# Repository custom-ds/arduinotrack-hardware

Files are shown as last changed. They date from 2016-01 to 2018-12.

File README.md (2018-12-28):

# ArduinoTrack APRS Tracker
The Project: Traveler ArduinoTrack flight controller is an Arduino-compatible board that includes a GPS, temp/pressure sensor, and options for a VHF transmitter module or a off-board transmitter.

For more information about the ArduinoTrack, visit the [Project: Traveler](https://www.projecttraveler.org/arduinotrack/arduinotrack-controller) website.

Firmware for the ArduinoTrack must be programmed via a hardware programmer.

[ArduinoTrack Firmware](https://github.com/custom-ds/arduinotrack-firmware)

## Buy an ArduinoTrack
Assembled ArduinoTracks can be purchased online from [Custom Digital Services](https://www.customdigitalservices.net/high-altitude-ballooning/buy-an-arduinotrack).

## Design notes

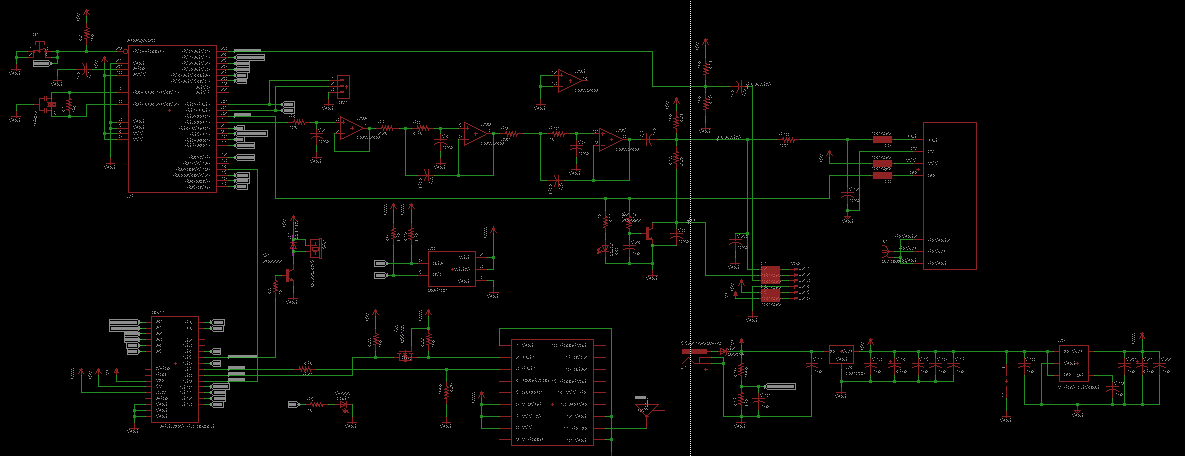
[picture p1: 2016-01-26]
ArduinoTrack Shield/arduinotrack_shield_v111-schematic.png

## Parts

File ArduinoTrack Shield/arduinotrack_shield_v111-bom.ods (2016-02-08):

Qty | Value | Device | Package | Parts | Description | DIGIKEY | SPARKFUN
1 |  | MA03-1 | MA03-1 | SV1 | PIN HEADER | 952-2264-ND
1 |  | TAC_SWITCHSMD | TACTILE_SWITCH_SMD | S1 | Momentary Switch | CKN9104CT-ND
14 | .1uF | C-USC0805 | C0805 | C1, C7, C9, C10, C11, C13, C15, C16, C17, C18, C19, C20, C22, C24 | CAPACITOR, American symbol | 311-1361-1-ND
1 | 100 | R-US_R0805 | R0805 | R18 | RESISTOR, American symbol | 311-100ARCT-ND
2 | 100k | R-US_R0805 | R0805 | R16, R20 | RESISTOR, American symbol | 311-100KCRCT-ND
7 | 10k | R-US_R0805 | R0805 | R2, R4, R14, R15, R22, R23, R24 | RESISTOR, American symbol | 311-10.0KCRCT-ND
6 | 10nF | C-USC0805 | C0805 | C2, C4, C6, C8, C12, C23 | CAPACITOR, American symbol | 399-1158-1-ND
8 | 160 ohm | SM-1206 | SM-1206 | L1, L2, L3, L4, L5, L6, L7, L8 | INDUCTOR | 240-2411-1-ND
1 | 16MHz | RESONATOR16MHZ | RESONATOR-SMD | Y1 | Resonator | 478-5420-1-ND
1 | 1M | R-US_R0805 | R0805 | R1 | RESISTOR, American symbol | 311-1.0MARCT-ND
5 | 1k | R-US_R0805 | R0805 | R3, R5, R10, R11, R12 | RESISTOR, American symbol | 311-1.0KARCT-ND
2 | 2.2k | R-US_R0805 | R0805 | R7, R13 | RESISTOR, American symbol | 311-2.2KARCT-ND
2 | 2N2222 | BC817-16LT1SMD | SOT23-BEC | Q1, Q2 | NPN Transistor | MMBT2222AFSCT-ND
1 | 390 | R-US_R0805 | R0805 | R9 | RESISTOR, American symbol | 311-390ARCT-ND
3 | 4.7k | R-US_R0805 | R0805 | R6, R8, R19 | RESISTOR, American symbol | 311-4.7KARCT-ND
2 | 47k | R-US_R0805 | R0805 | R17, R21 | RESISTOR, American symbol | 311-47.0KCRCT-ND
2 | 47nF | C-USC0805 | C0805 | C3, C5 | CAPACITOR, American symbol | 399-1166-1-ND
2 | 47uF | CPOL-US153CLV-0605 | 153CLV-0605 | C14, C21 | POLARIZED CAPACITOR, American symbol | PCE3842CT-ND
1 | 5.5x2.1mm Barrel | POWER_JACKSMD | POWER_JACK_SMD | J1 | Power Jack | CP-002AHPJCT-ND
1 | ARDUINO_R3_SHIELD | ARDUINO_R3_SHIELD | UNO_R3_SHIELD | SH11 | Shield form compatible with the Arduino Uno R3. |  | PRT-10007
1 | ATMega328 | MEGA8-AI | TQFP32-08 | U7 | MICROCONTROLLER | ATMEGA328P-15AZCT-ND
1 | B220/A | B340A | SMA-DIODE | D2 | Schottky Diode | 641-1258-1-ND
1 | BMP180 | BMP180 | BMP180 | U8 | BOSCH BMP180 DIGITAL BAROMETRIC PRESSURE SENSOR |  | COM-11823
1 | BSS138 | BSS138 | BSS138 | Q3 | BSS138 | BSS138CT-ND
1 | BU-SMA-H | BU-SMA-H | BU-SMA-H | X1 | FEMALE SMA CONNECTOR | CONSMA001-ND
1 | BUZZERNS | BUZZERNS | BUZZER-12MM-NS | SG1 | Buzzer 12mm | 102-1155-ND
1 | GPS_ANT_SMDBAR | GPS_ANT_SMDBAR | 1575AT43A40 | ANT1 | 1.575 GHz GPS Antenna Johanson Technology | 712-1003-1-ND
1 | Green | LEDCHIPLED_1206 | CHIPLED_1206 | LED1 | LED | 160-1169-1-ND
1 | LL4148 | DIODE-MINIMELF | MINIMELF | D1 | DIODE | 568-1749-1-ND
1 | LM1086 | LM1086TO263 | TO263 | U4 |  | LM1086ISX-5.0/NOPBCT-ND
1 | MCP6L04T-E/SL | MCP6L04T-E/SL | SO14 | U9 | Rail-to-Rail Output Operational Amplifiers | MCP6L04T-E/SLCT-ND
1 | HX1-144.390-3 | RADIOMETRIX-HX1 | RADIOMETRIX-HX1 | U5
1 | Red | LEDCHIPLED_1206 | CHIPLED_1206 | LED2 | LED | 160-1405-1-ND
1 | UBLOX MAX-M8Q | UBLOX_MAX | UBLOX_MAX | U3 | UBLOX MAX
1 | VHF | 22-05-7068-06 | 7395-06 | J2 | CONNECTOR | WM4304-ND
1 | V_REG_LDOSMD | V_REG_LDOSMD | SOT23-5 | U6 | Voltage Regulator LDO | LP3985IM5-3.3/NOPBCT-ND

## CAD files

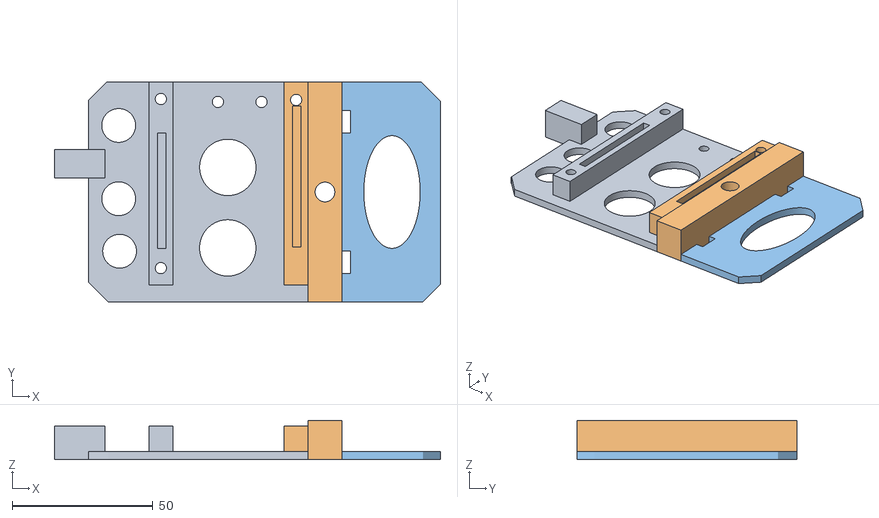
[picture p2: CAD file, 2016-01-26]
Cases/combined/combined.stl
137.0 x 78.0 x 14.0

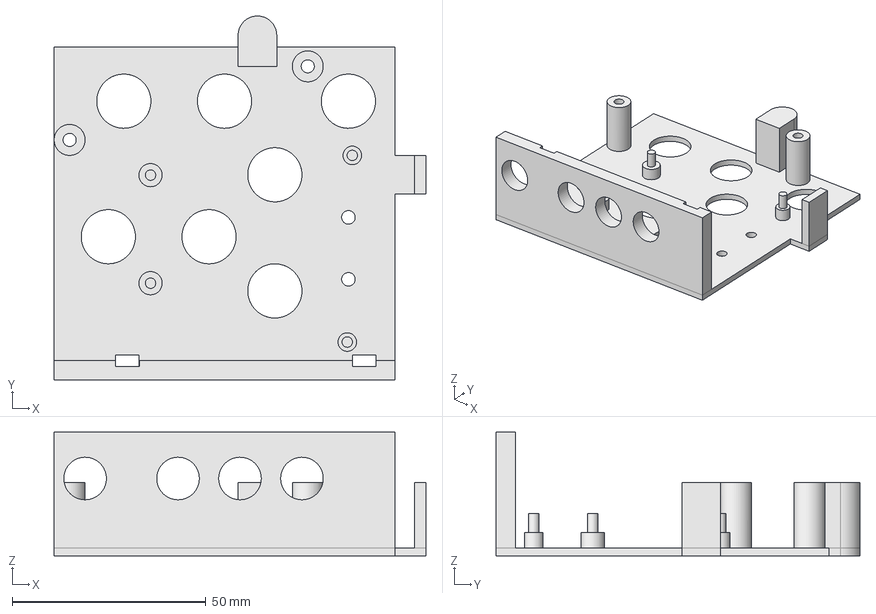
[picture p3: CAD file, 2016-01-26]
Cases/Open Frame for Shield.FCStd
96.0 x 94.0 x 32.0 mm

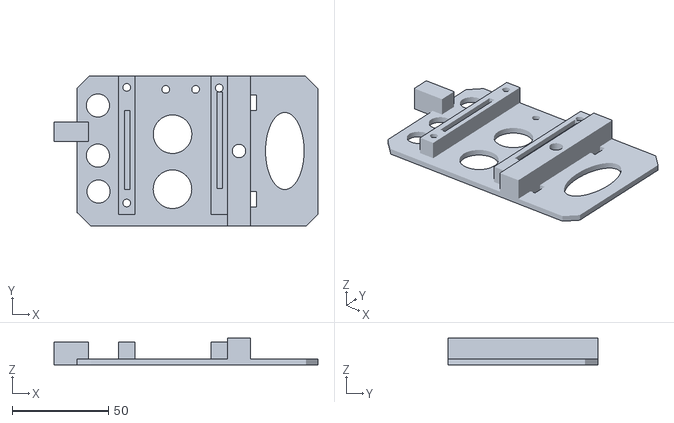
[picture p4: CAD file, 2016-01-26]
Cases/combined/combined2.stl
137.0 x 78.0 x 14.0

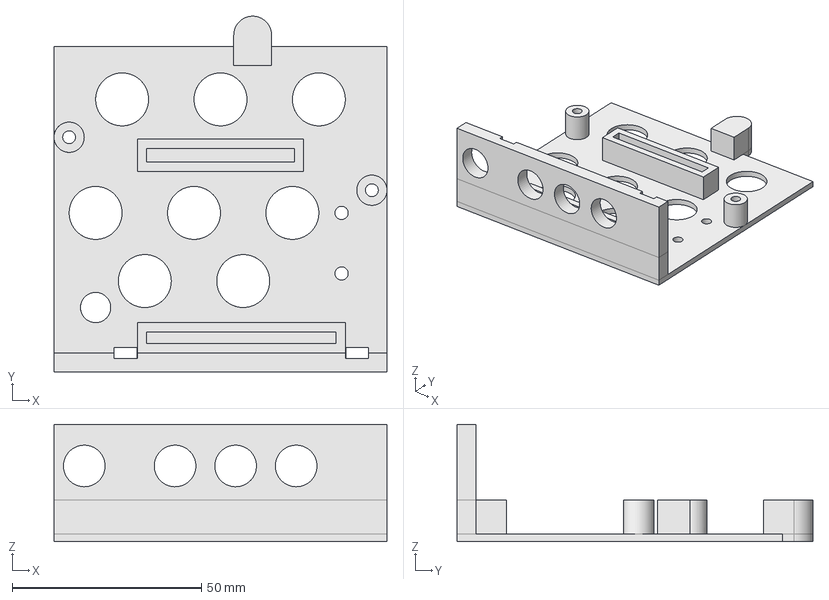
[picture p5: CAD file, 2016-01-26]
Cases/Open Frame for Combined.FCStd
88.0 x 94.0 x 31.0 mm

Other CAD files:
Cases/Open Frame for Combined.stl
Cases/Open Frame for Shield.stl

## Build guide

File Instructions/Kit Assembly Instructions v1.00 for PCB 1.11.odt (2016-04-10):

ArduinoTrack Assembly

Version 1.0 for PCB Version 1.11

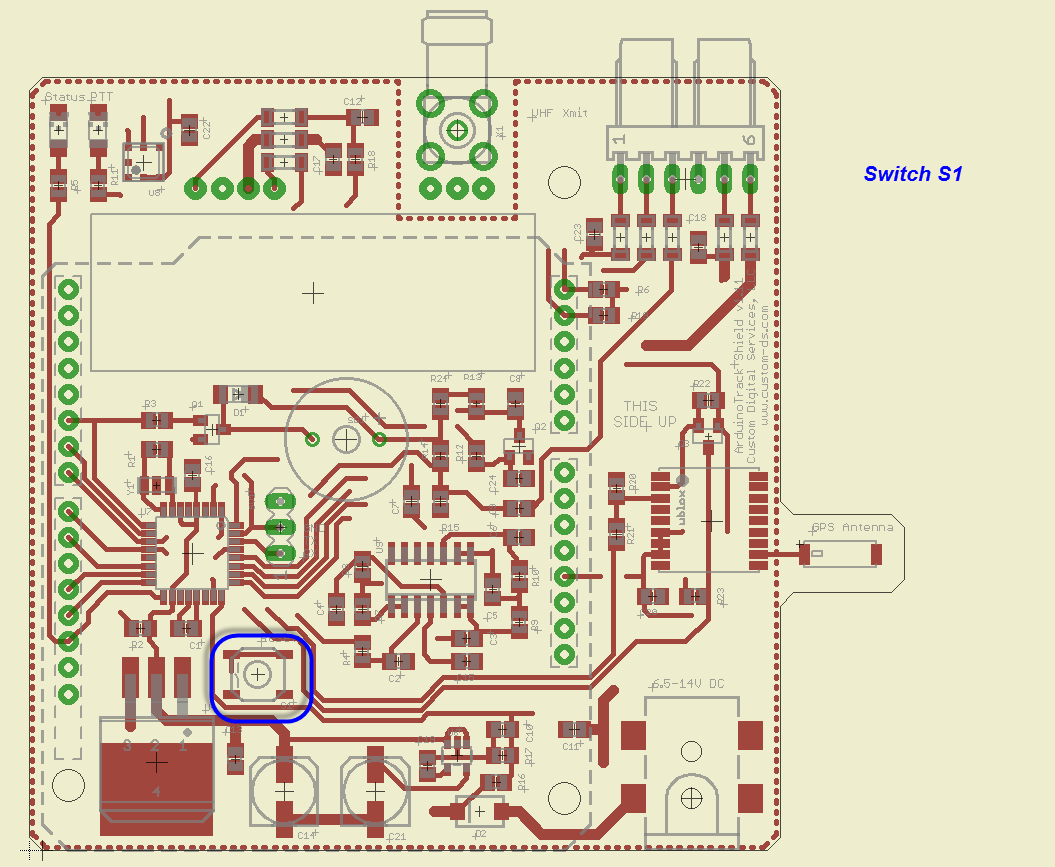
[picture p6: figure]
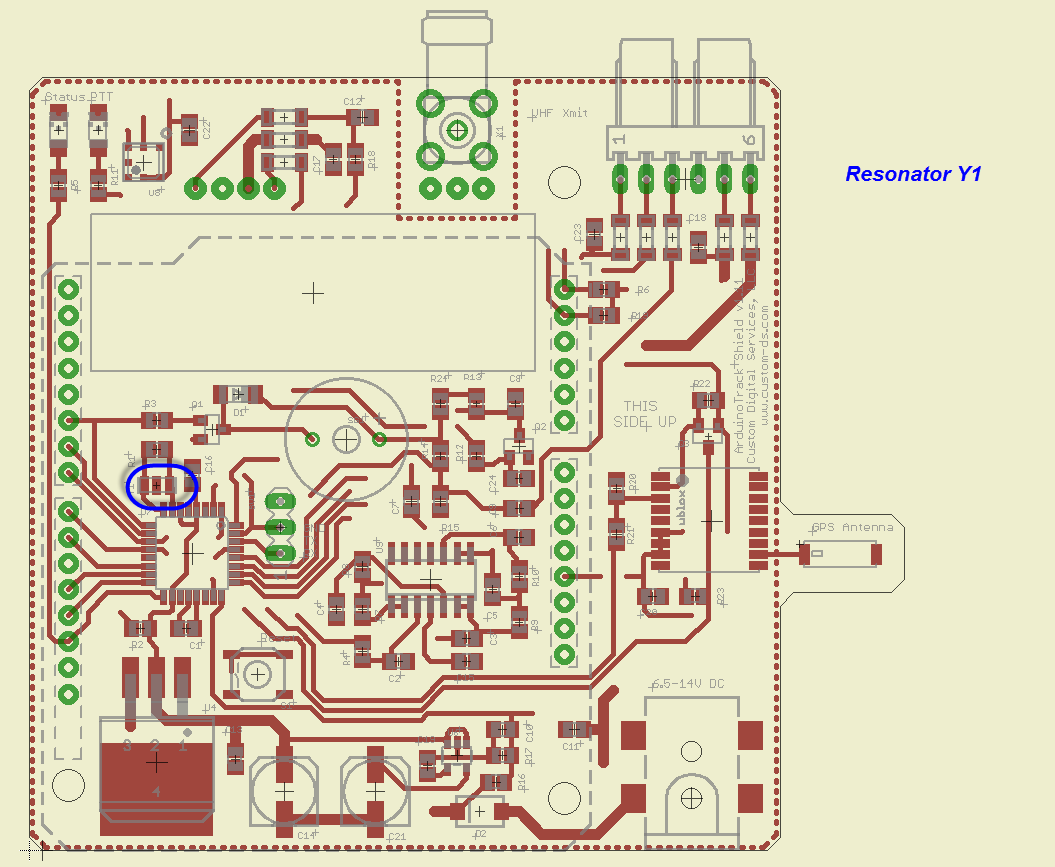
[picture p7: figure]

Switch S1 | Resonator Y1

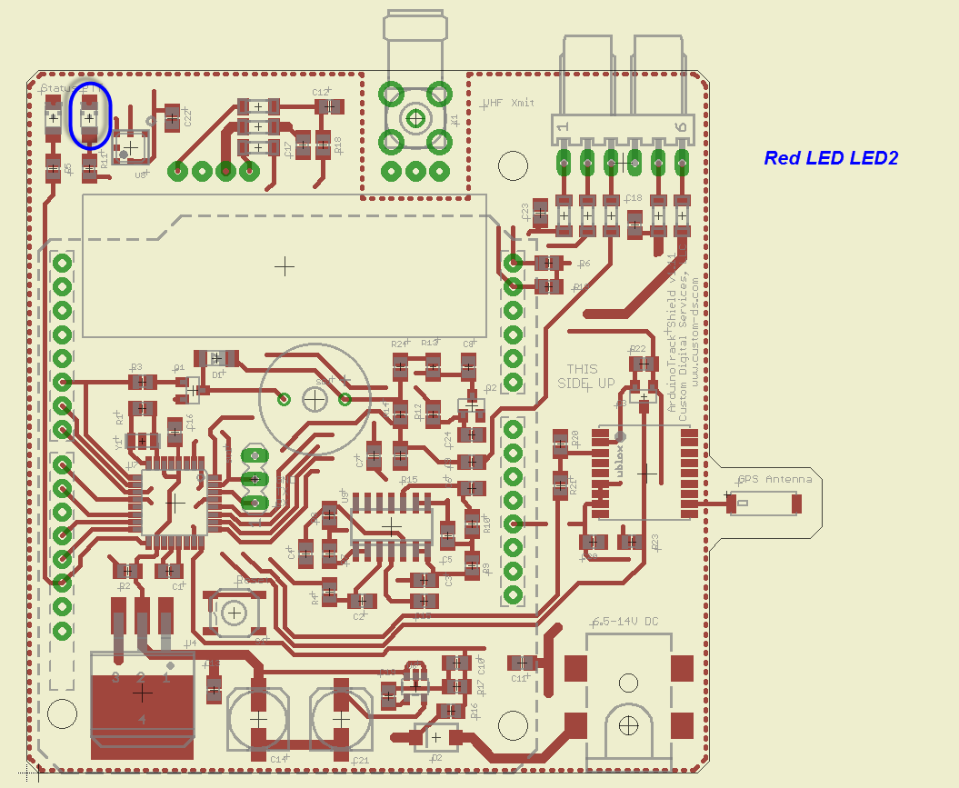
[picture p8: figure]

Green LED LED1 | Red LED LED2

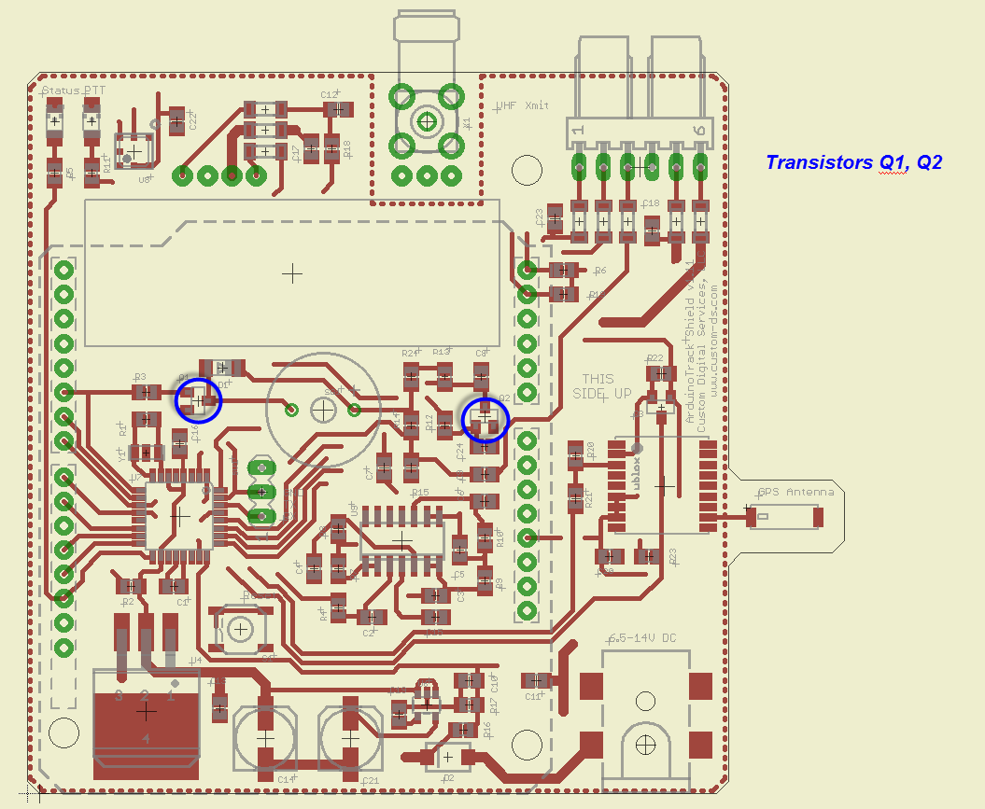
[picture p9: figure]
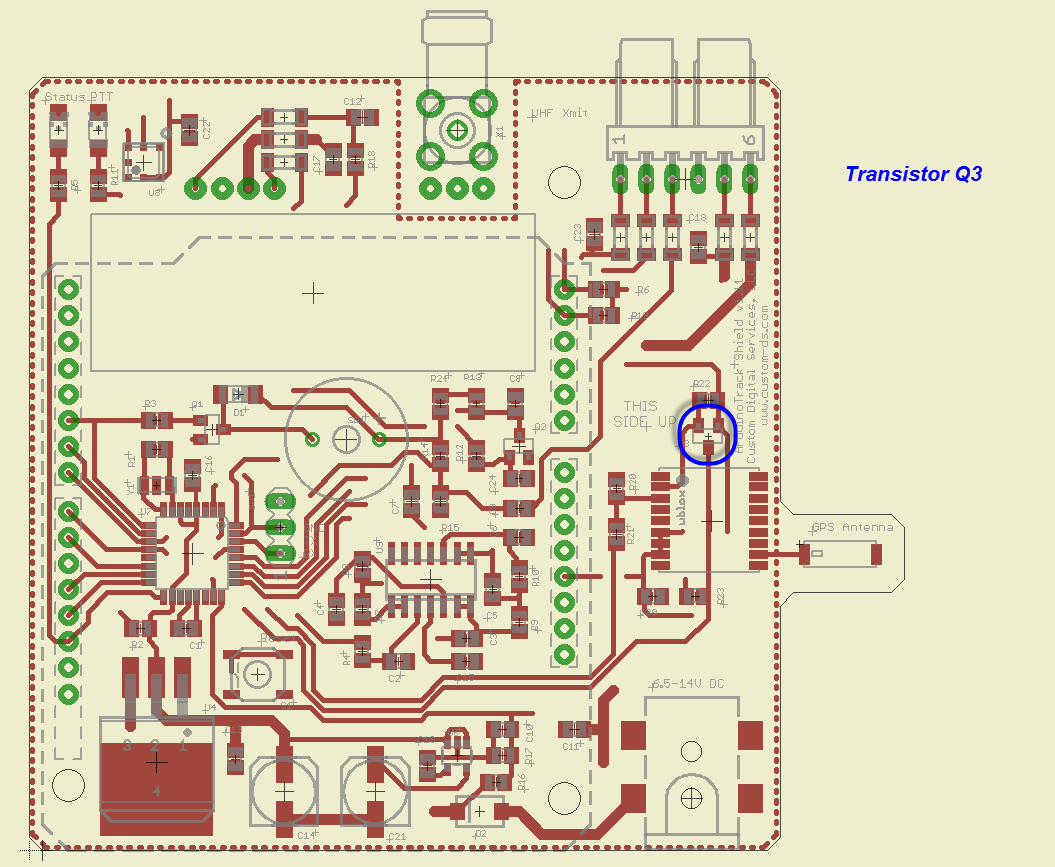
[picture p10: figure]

Transistors Q1, Q2 | FET Transistor Q3

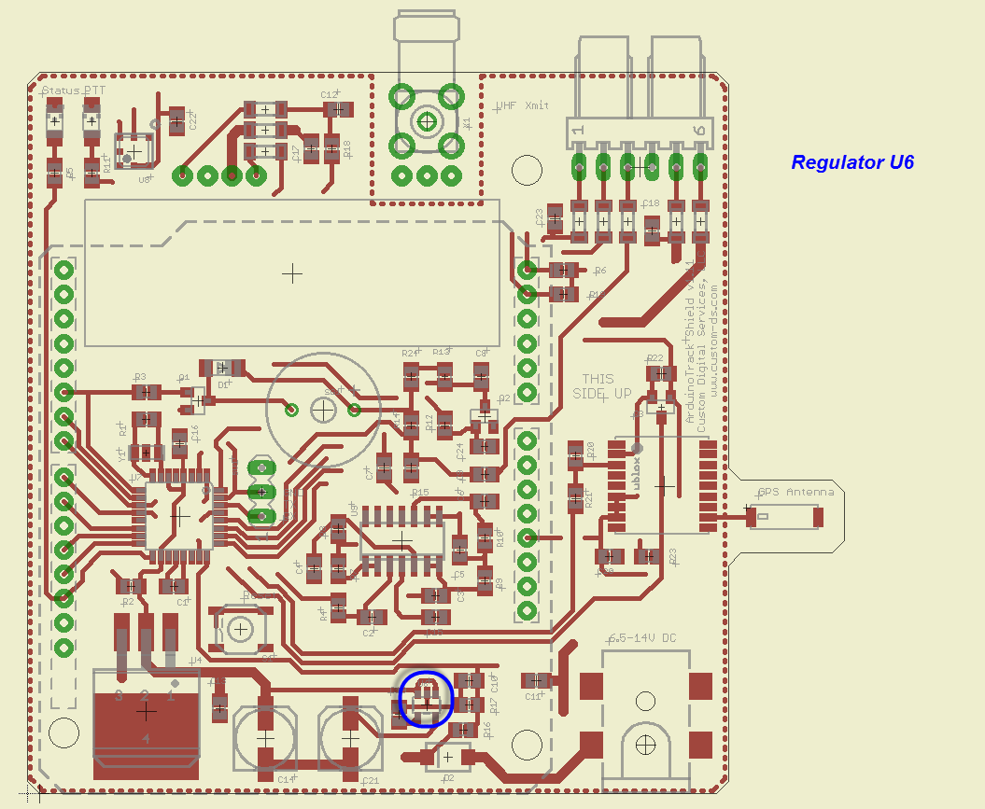
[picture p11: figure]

3.3V Regulator U6 | GPS Antenna ANT1

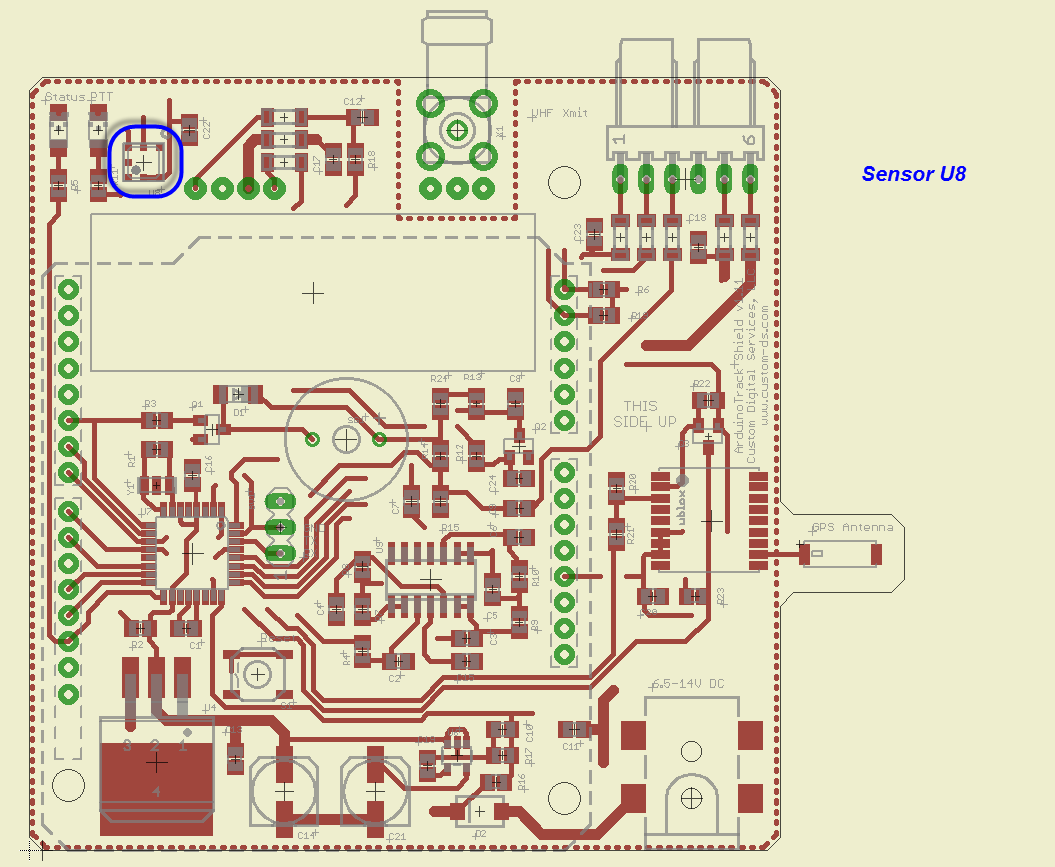
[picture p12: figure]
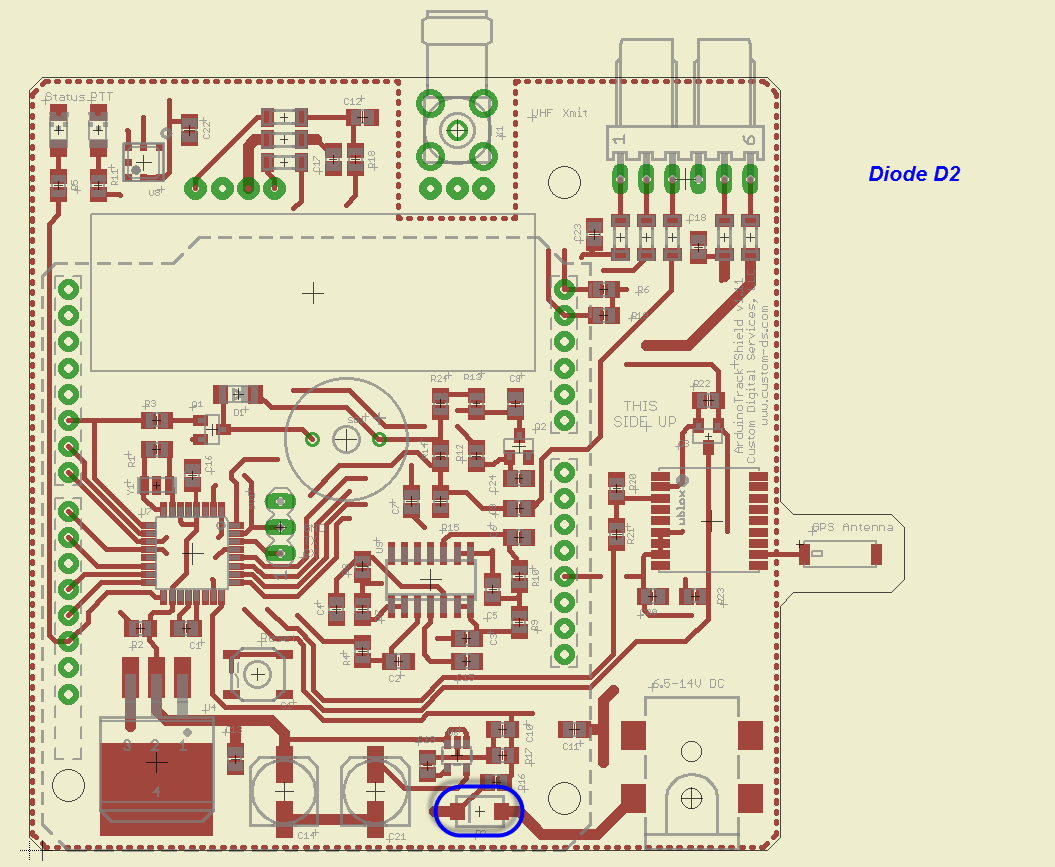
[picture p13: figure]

BMP180 Temp/Baro Sensor U8 | Schottky Protection Diode D2

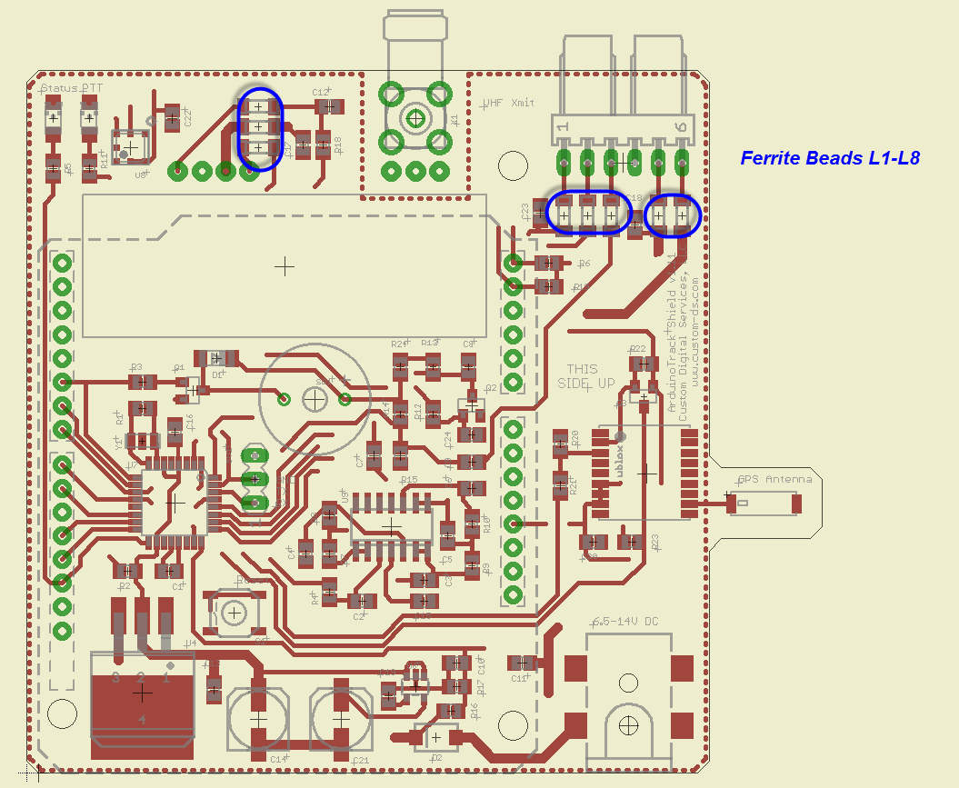
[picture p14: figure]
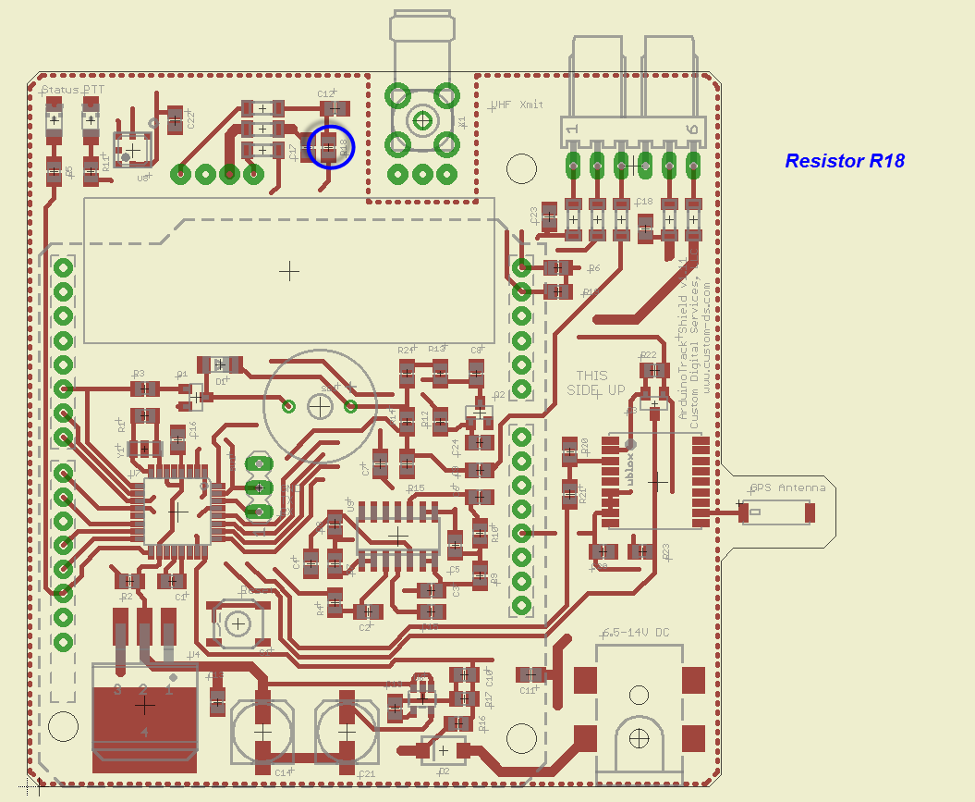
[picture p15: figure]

Ferrite Beads L1-L8 | 100Ω Resistor R18

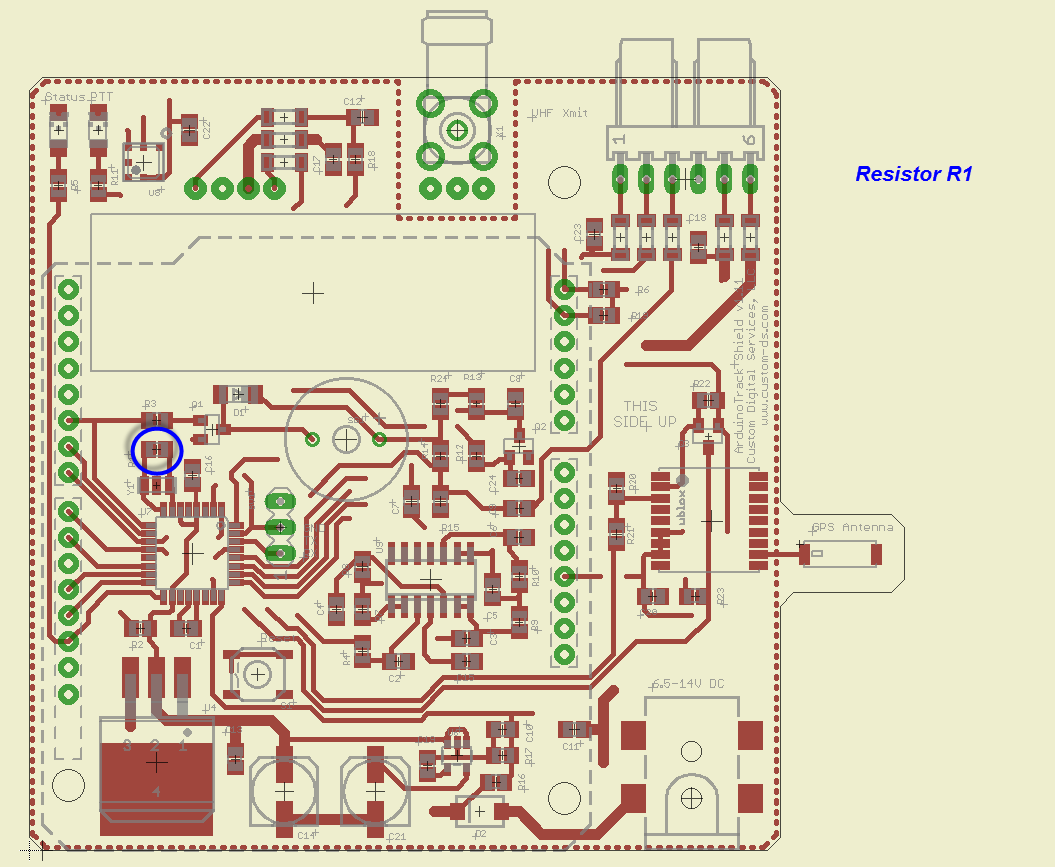
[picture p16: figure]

390Ω Resistor R9 | 1M Resistor R1

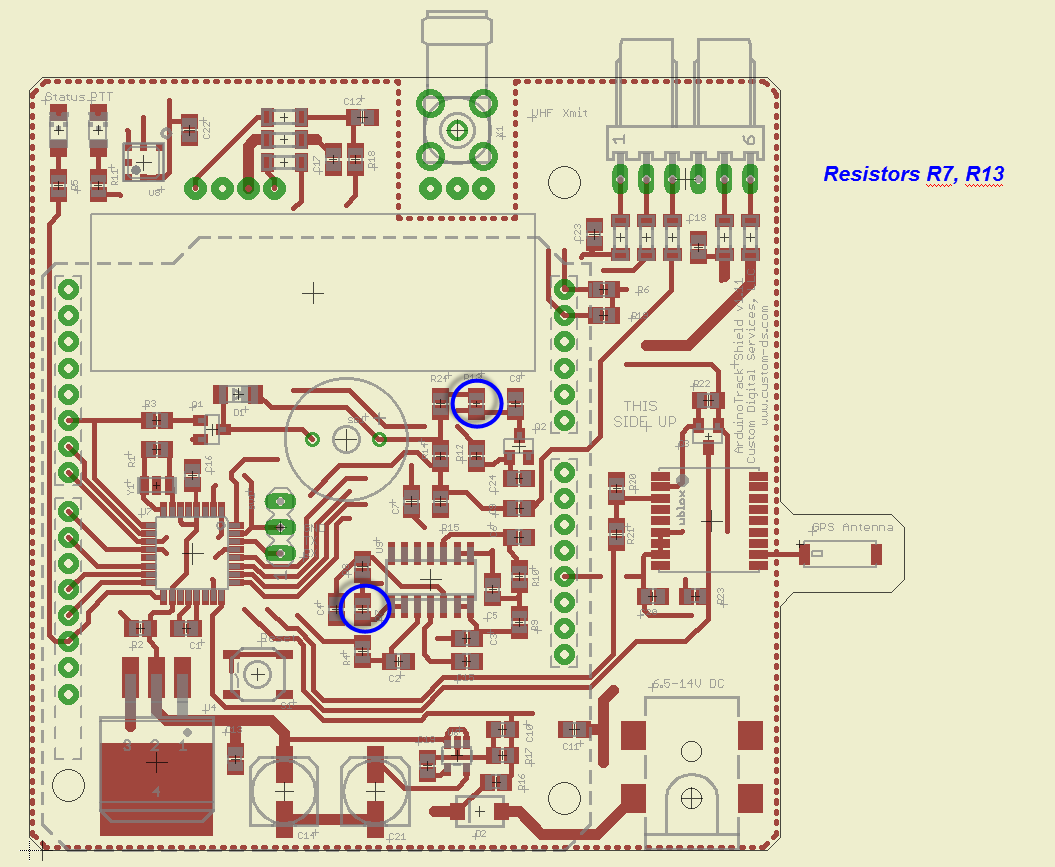
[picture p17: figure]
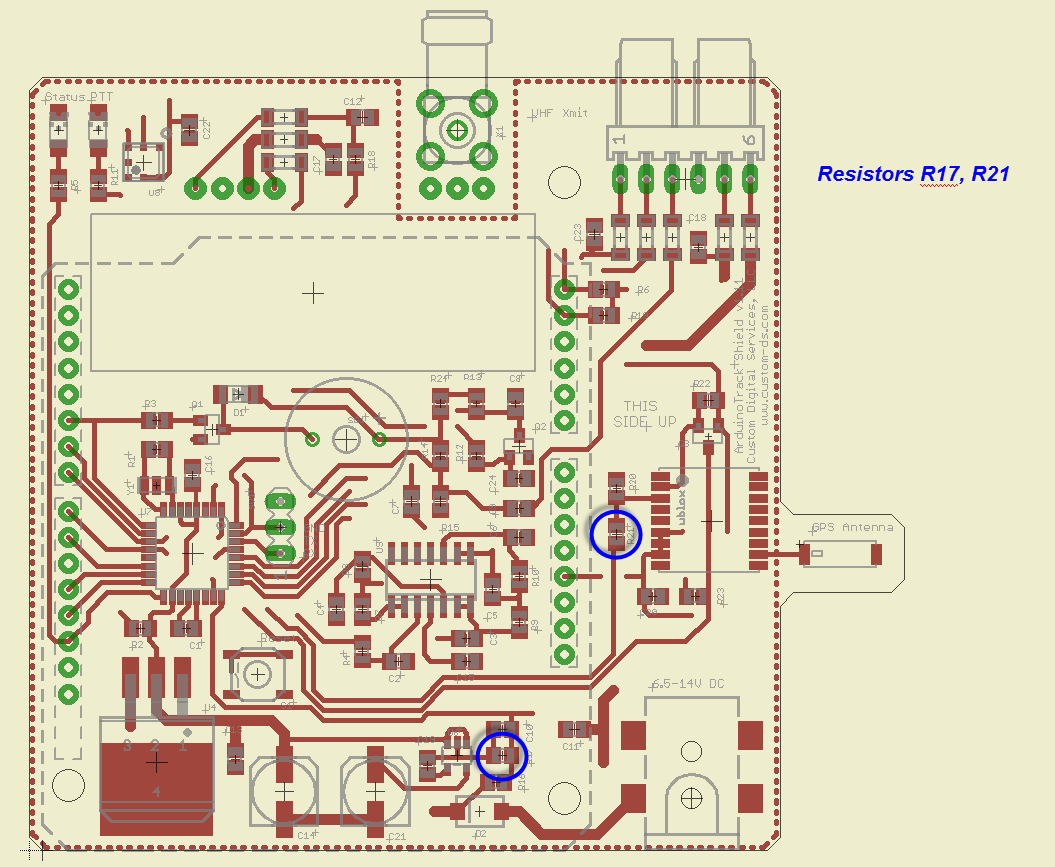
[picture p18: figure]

2.2k Resistors R7, R13 | 47k Resistors R17, R21

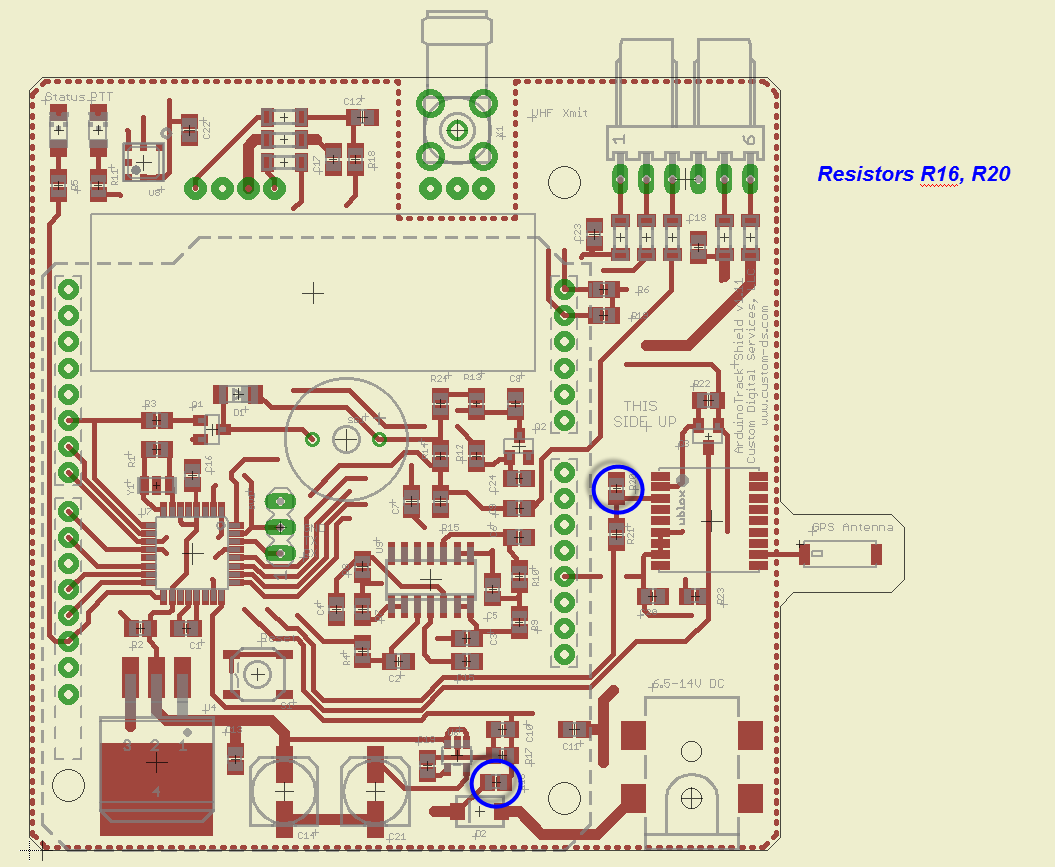
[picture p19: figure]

100k Resistors R16, R20 | 4.7k Resistors R6, R8, R19

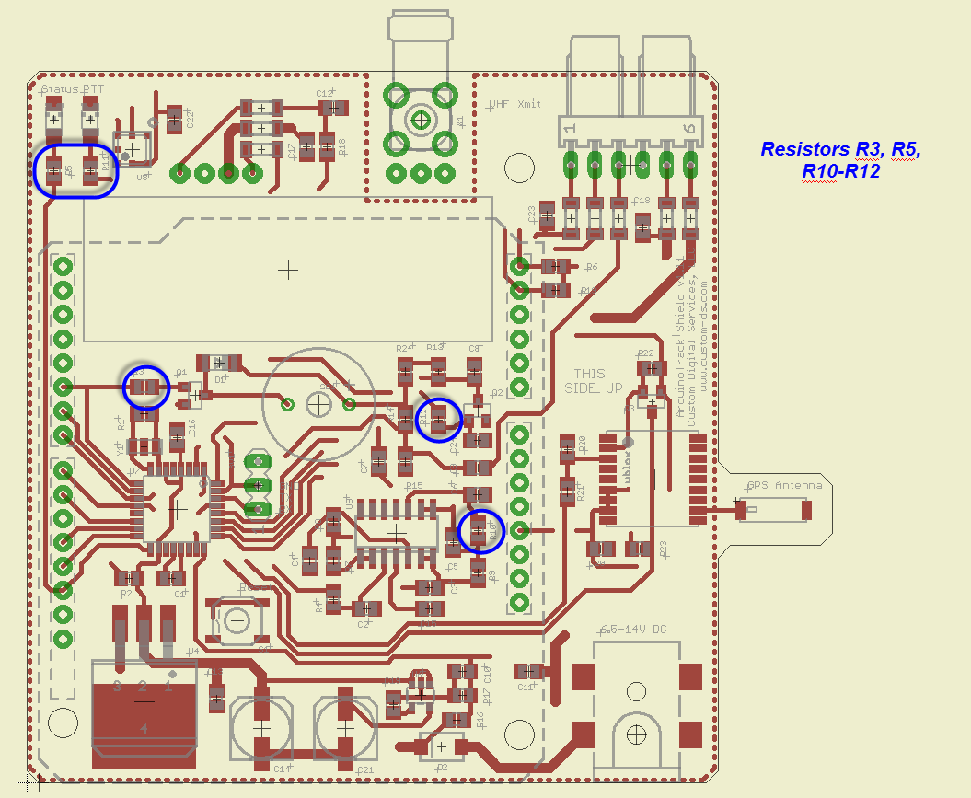
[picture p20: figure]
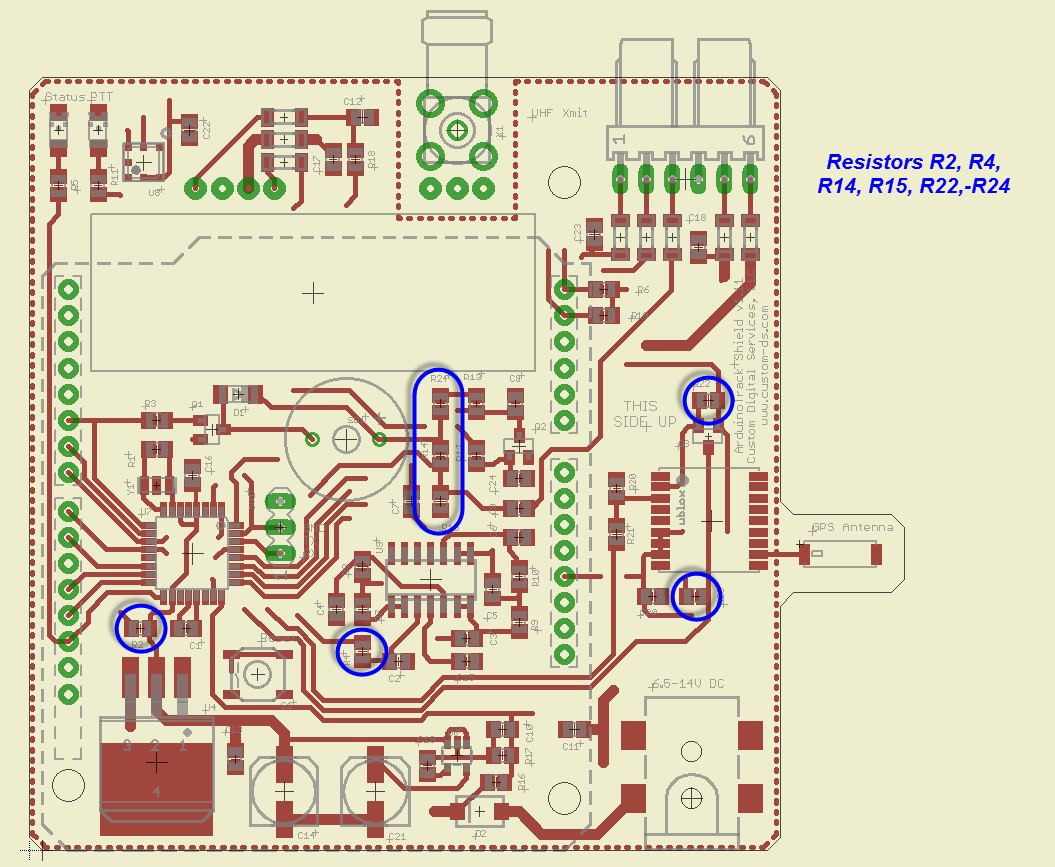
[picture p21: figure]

1k Resistors R3, R5, R10-R12 | 10k Resistors R2, R4, R14, R15, R22-R24

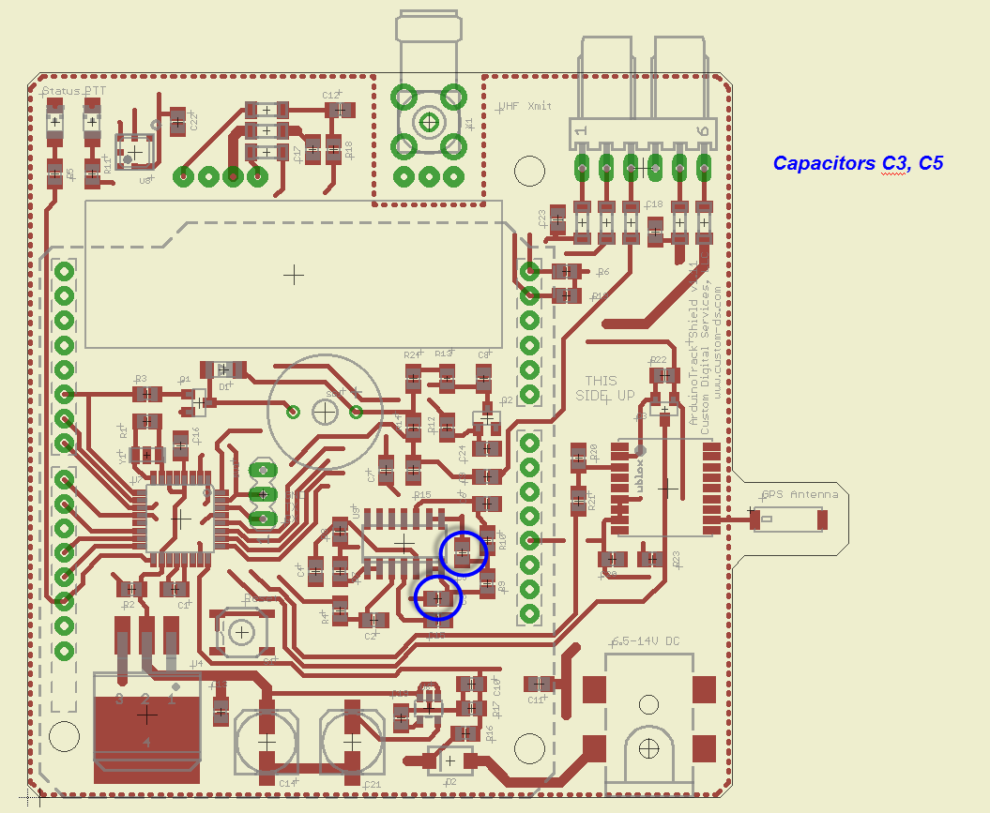
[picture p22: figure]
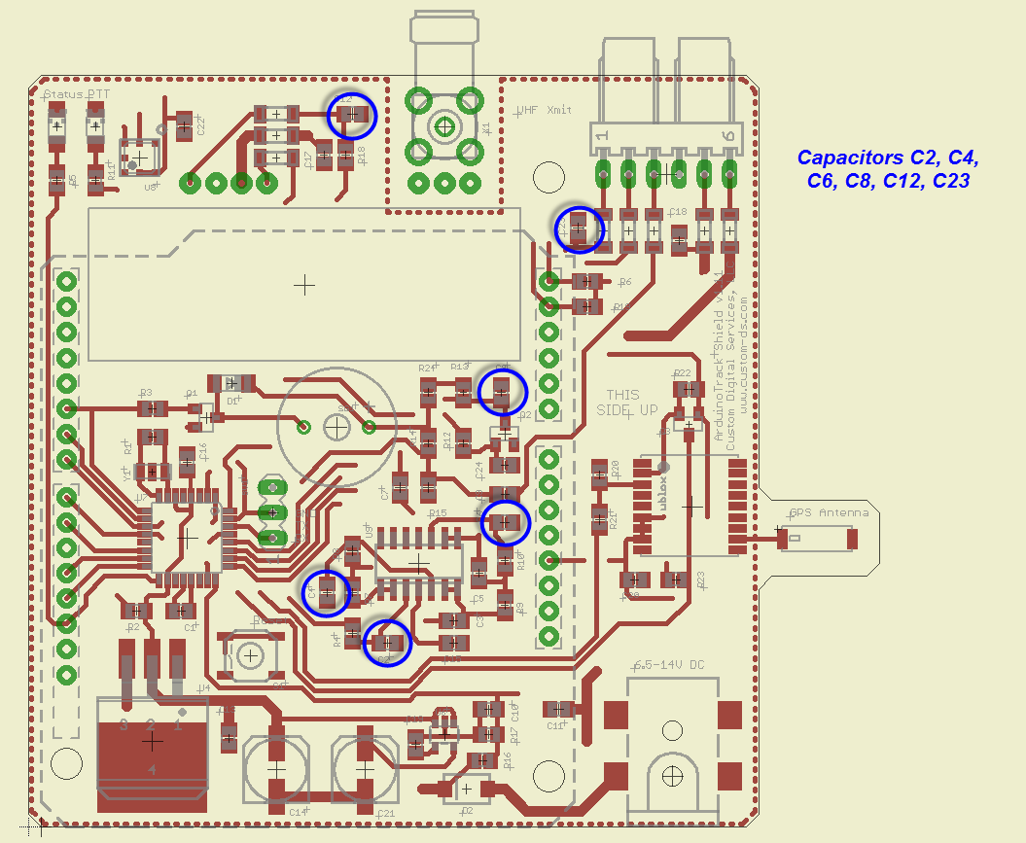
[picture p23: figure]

47nF Capacitors C3, C5 | 10nF Capacitors C2, C4, C6, C8, C12, C23

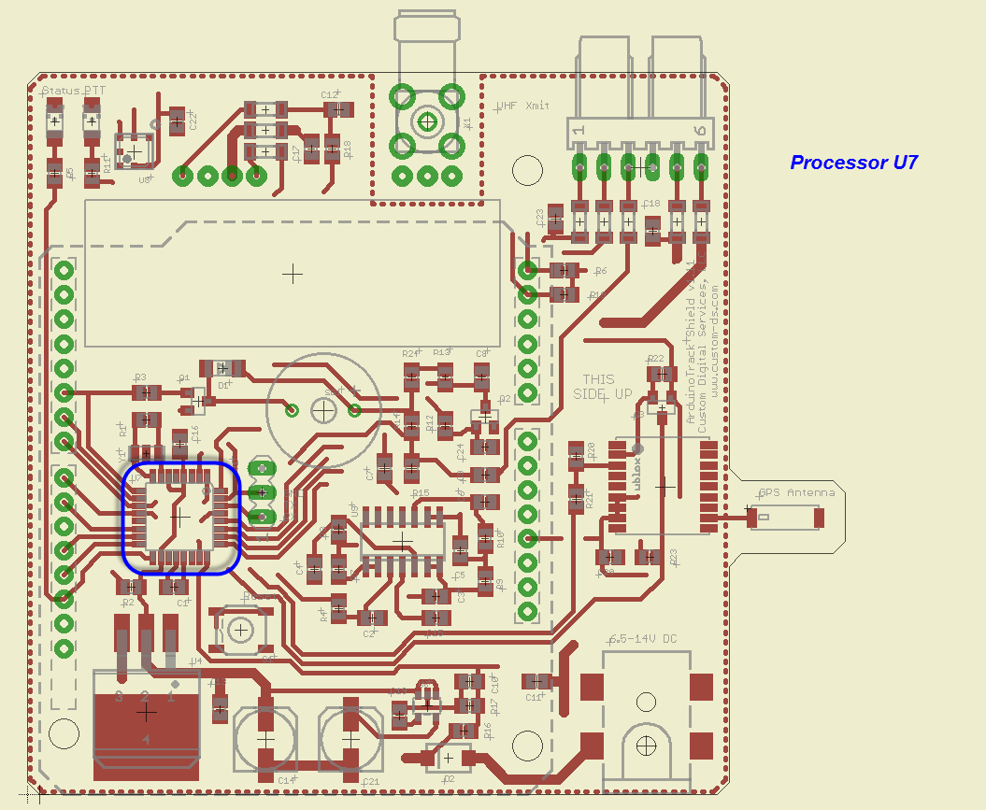
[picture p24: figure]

.1μF Capacitors C1, C7, C9-C11, C15-C20, C22, C24 | ATMega328p μController U7

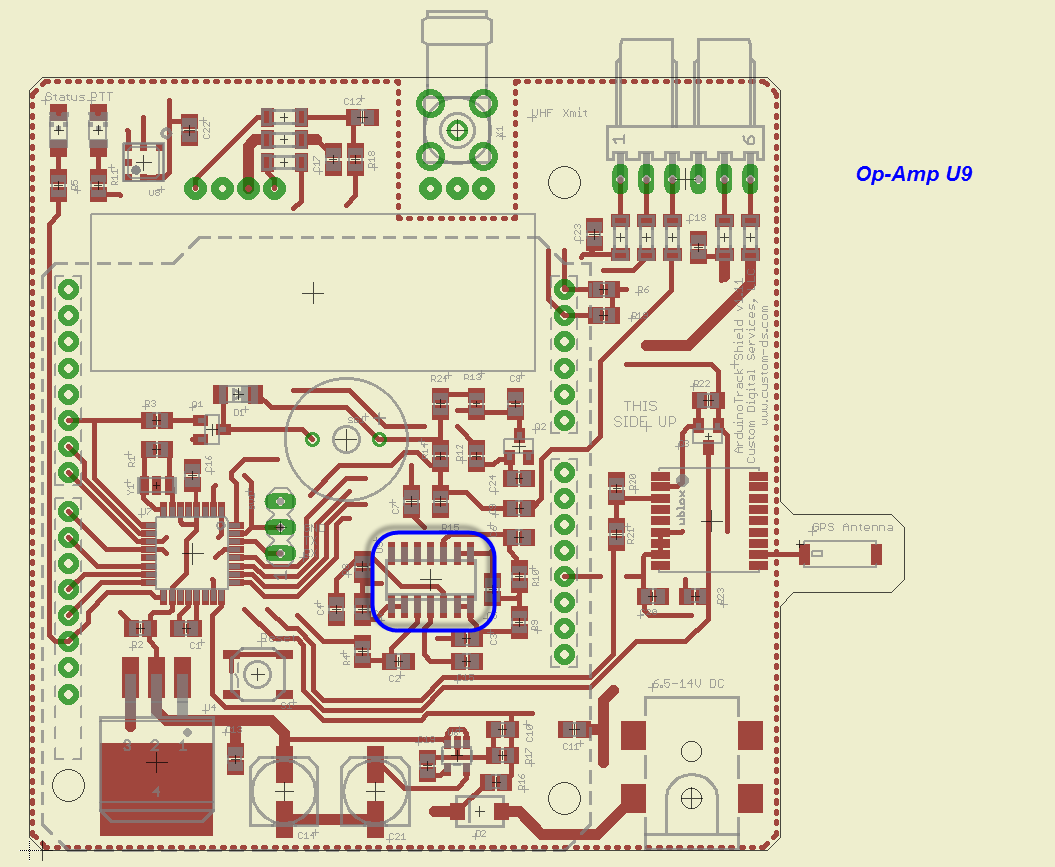
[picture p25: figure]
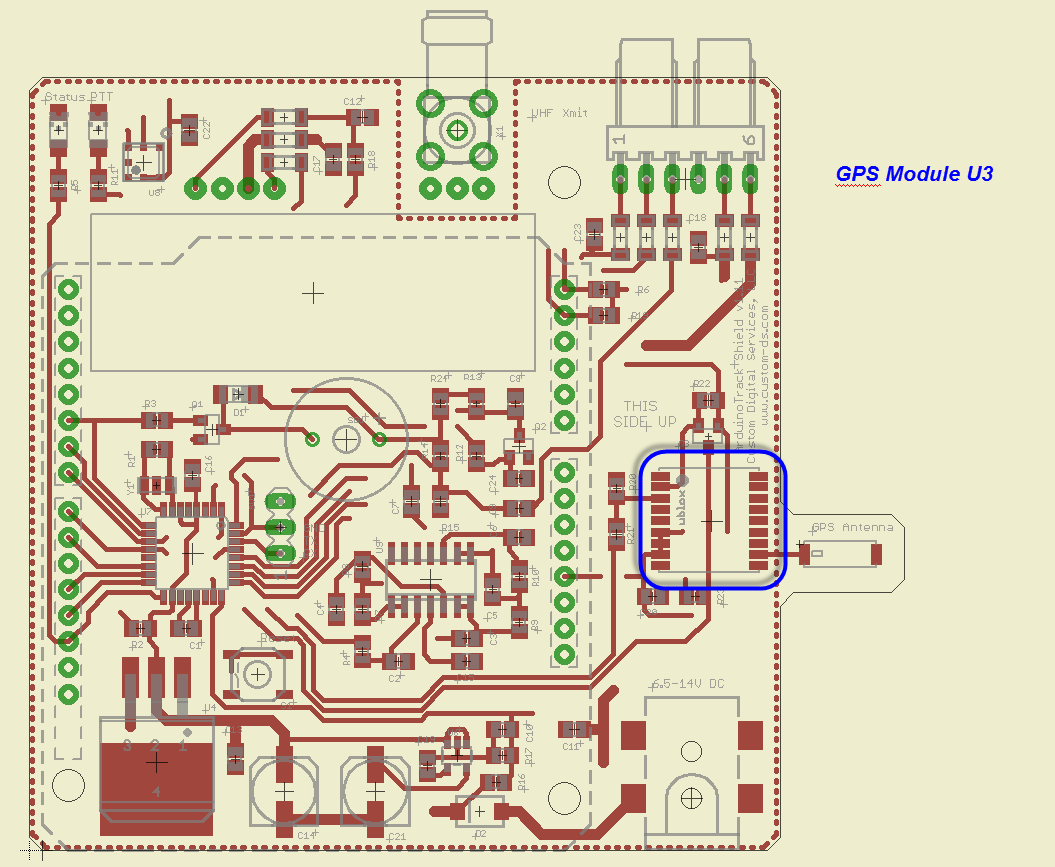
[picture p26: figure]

MCP6L04T Op-Amp U9 | uBlox MAX-M8Q GPS Module U3

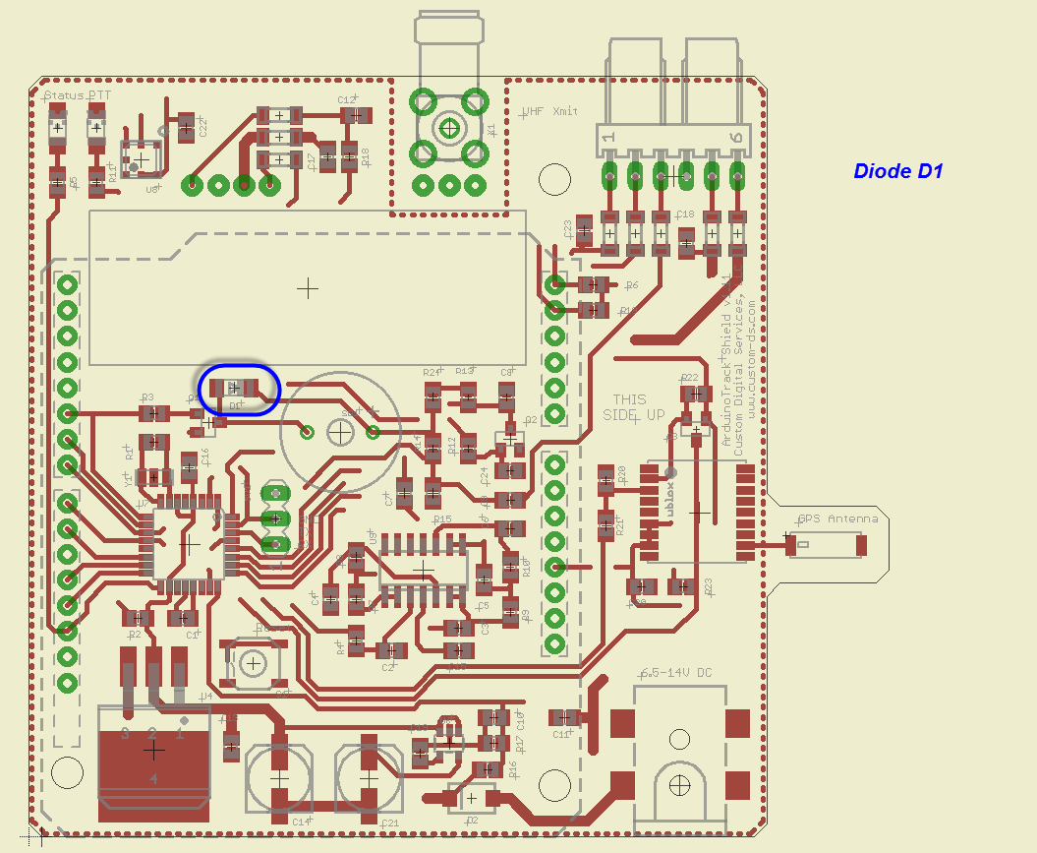
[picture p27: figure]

Diode D1 | 5V Regulator U4

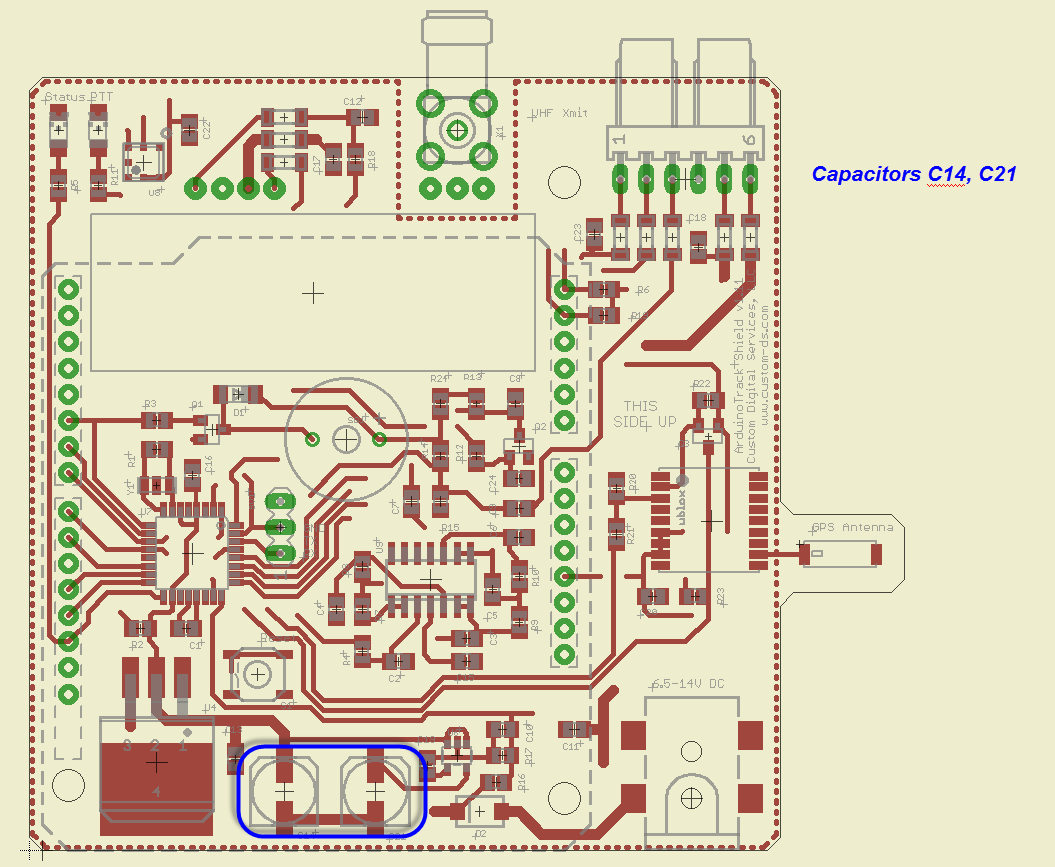
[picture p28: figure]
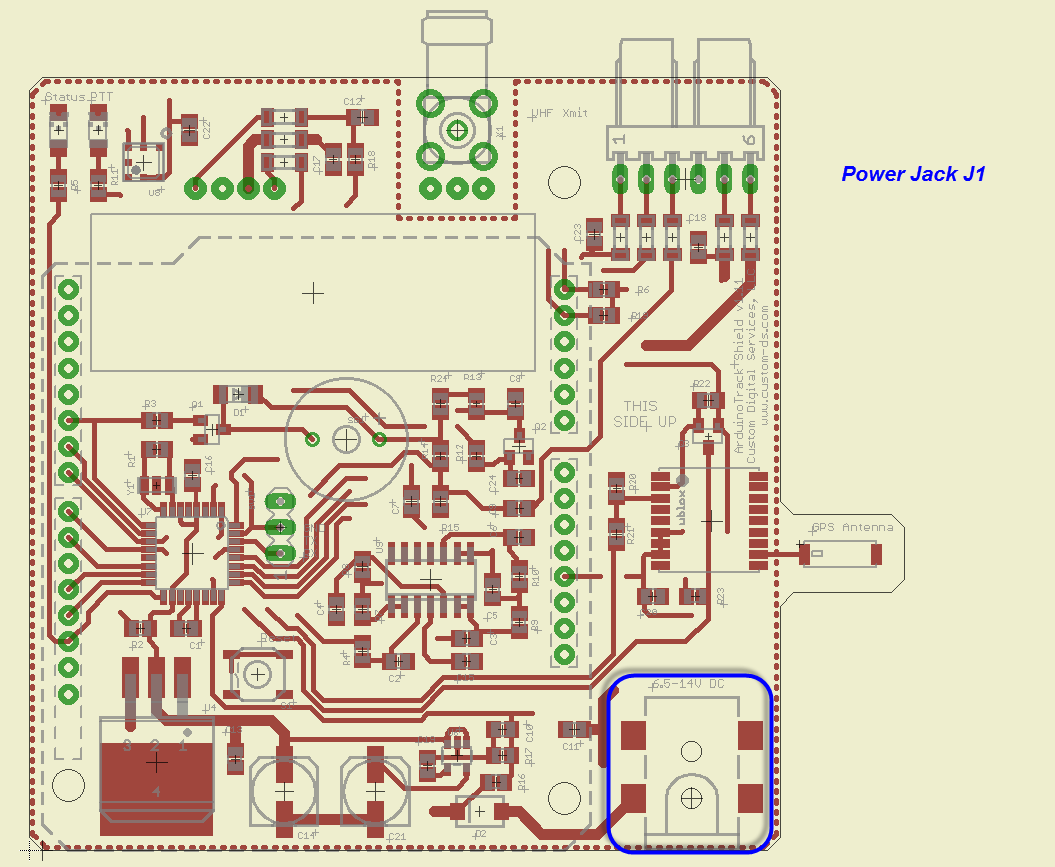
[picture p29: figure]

47μF Electrolytic Capacitors C14, C21 | Power Jack J1

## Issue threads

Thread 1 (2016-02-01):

Insert resistors in series with Configuration header and/or pin 0/1

custom-ds, 2016-02-01:
Could possibly eliminate the errors when trying to run the Arduino-Combined while it is still attached to it programming host.  Currently it behaves badly until it is removed from the host.

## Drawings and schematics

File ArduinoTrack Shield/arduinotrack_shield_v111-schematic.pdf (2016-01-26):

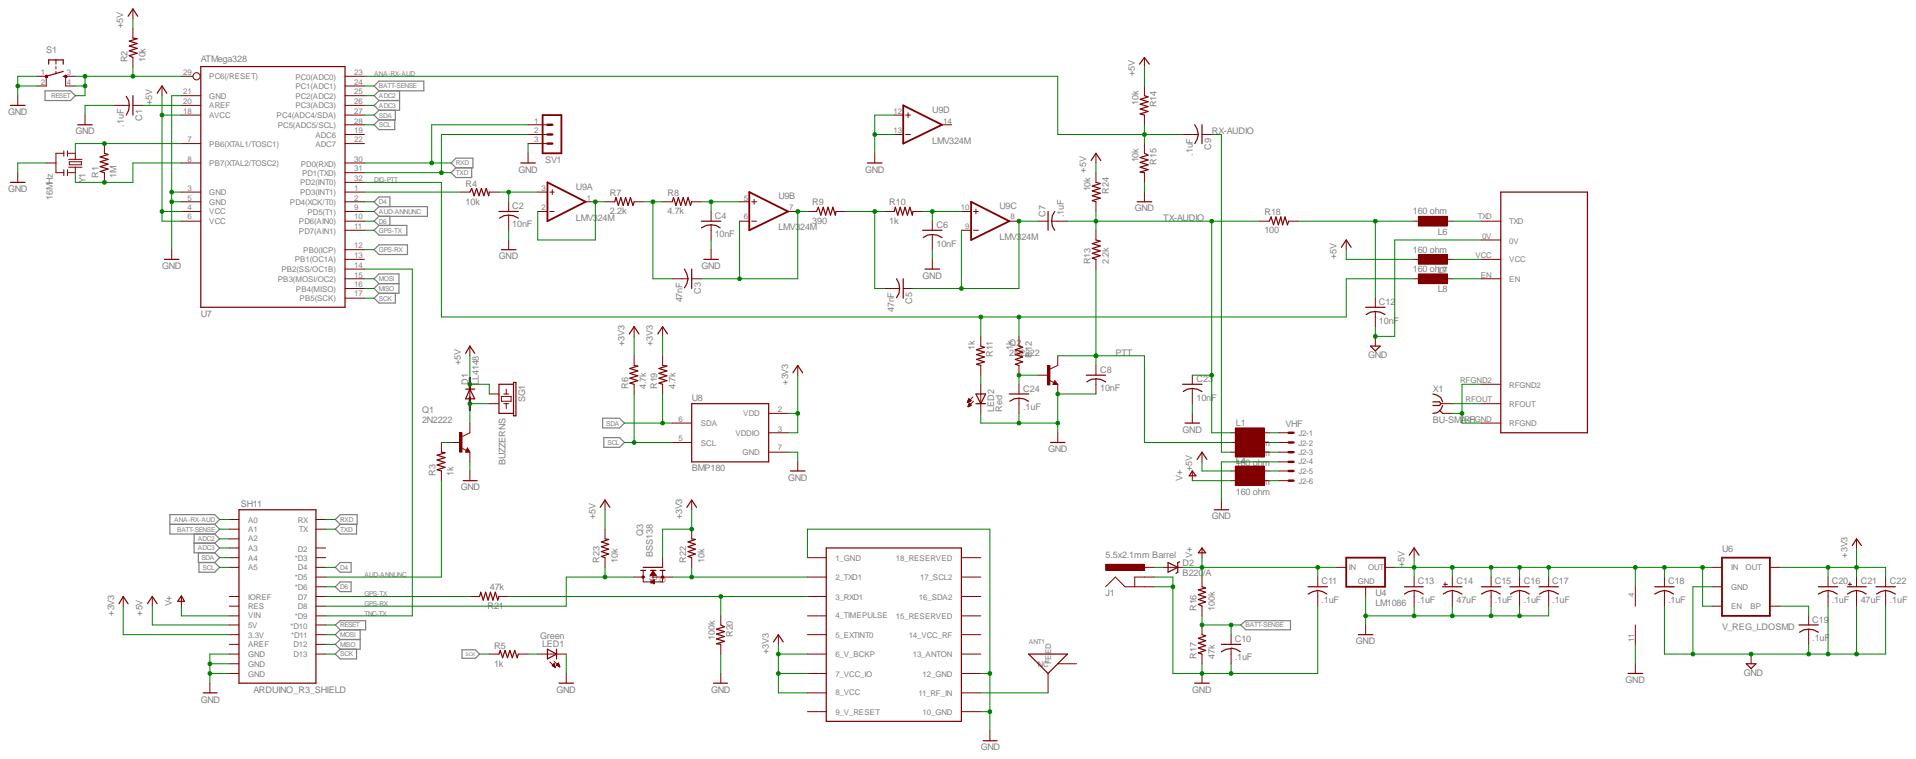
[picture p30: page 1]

5 | RXD TXD

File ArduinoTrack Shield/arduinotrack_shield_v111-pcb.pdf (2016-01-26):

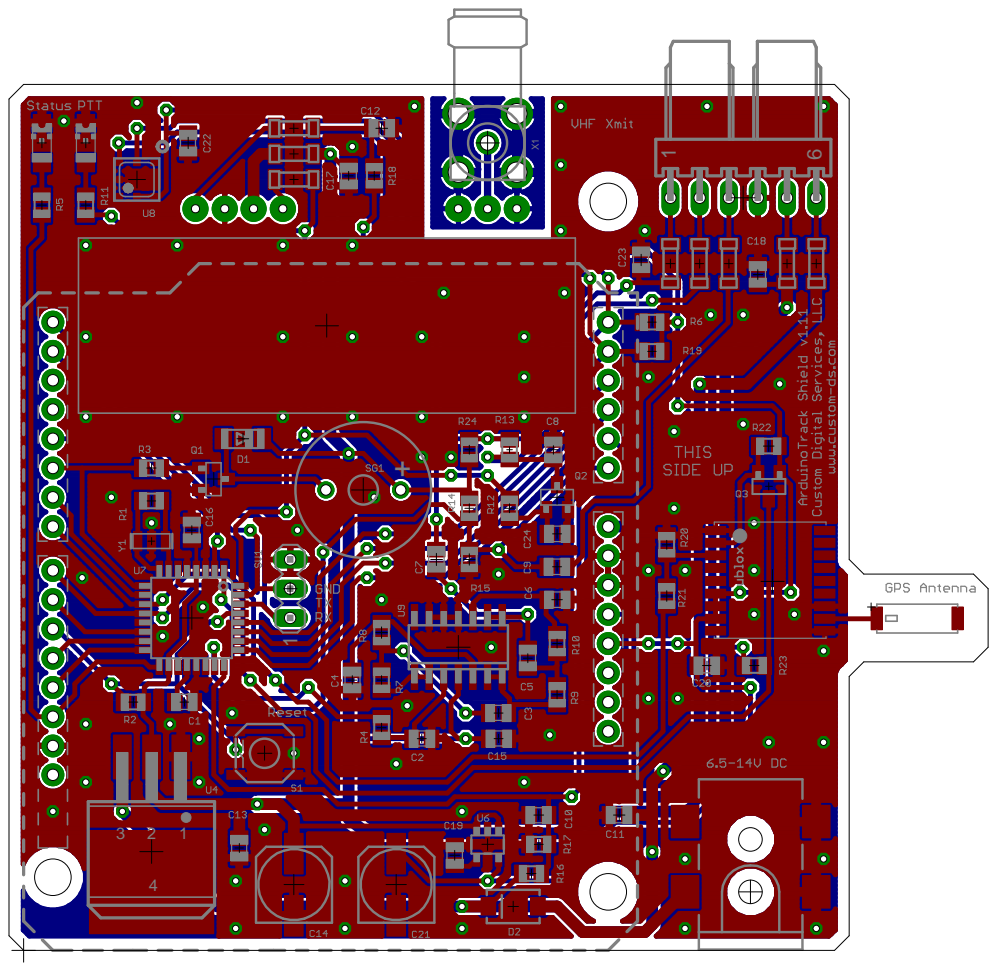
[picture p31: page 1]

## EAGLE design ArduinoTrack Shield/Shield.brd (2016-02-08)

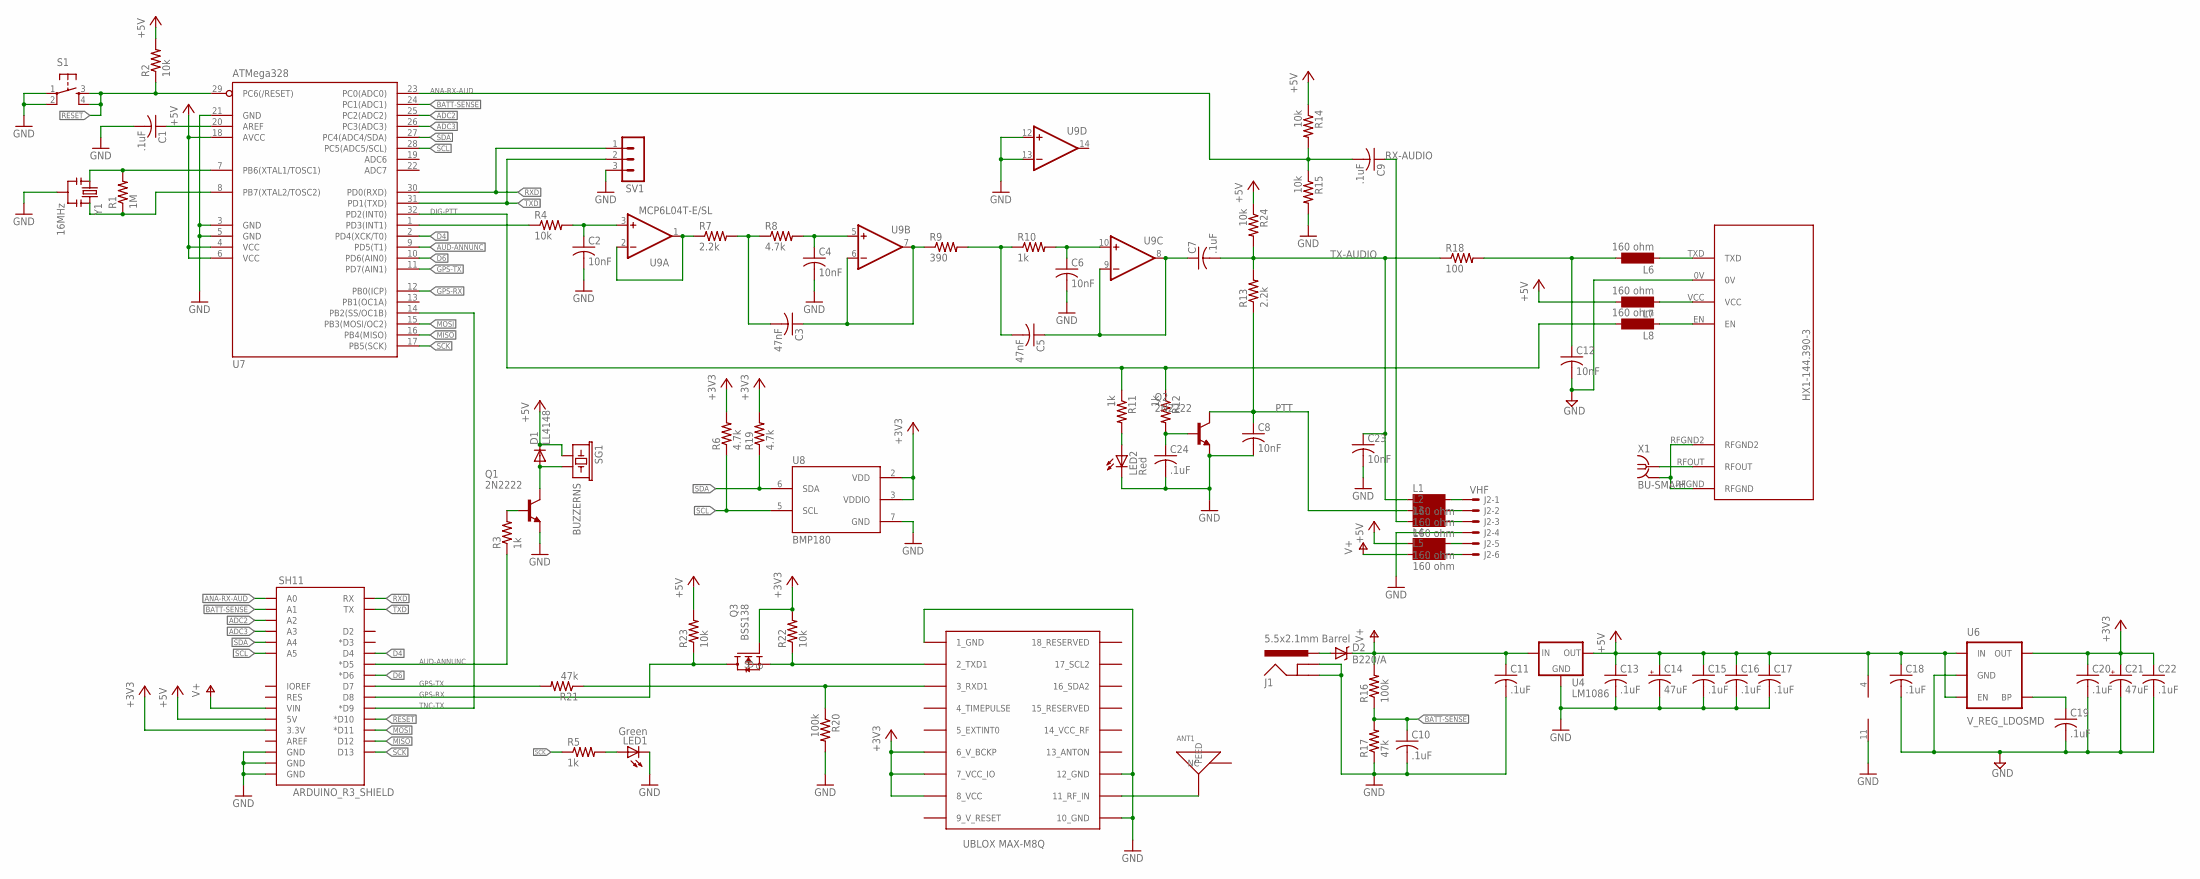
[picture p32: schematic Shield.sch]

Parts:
ANT1: GPS_ANT_SMDBAR; 1575AT43A40; DIGIKEY 712-1003-1-ND
C1, C7, C9, C10, C11, C13, C15, C16, C17, C18, C19, C20, C22, C24: .1uF; C0805; DIGIKEY 311-1361-1-ND
C2, C4, C6, C8, C12, C23: 10nF; C0805; DIGIKEY 399-1158-1-ND
C3, C5: 47nF; C0805; DIGIKEY 399-1166-1-ND
C14, C21: 47uF; 153CLV-0605; DIGIKEY PCE3842CT-ND
D1: LL4148; MINIMELF; DIGIKEY 568-1749-1-ND
D2: B220/A; SMA-DIODE; DIGIKEY 641-1258-1-ND
J1: 5.5x2.1mm Barrel; POWER_JACK_SMD; DIGIKEY CP-002AHPJCT-ND
J2: VHF; 7395-06; DIGIKEY WM4304-ND
L1, L2, L3, L4, L5, L6, L7, L8: 160 ohm; SM-1206; DIGIKEY 240-2411-1-ND
LED1: Green; CHIPLED_1206; DIGIKEY 160-1169-1-ND
LED2: Red; CHIPLED_1206; DIGIKEY 160-1405-1-ND
Q1, Q2: 2N2222; SOT23-BEC; DIGIKEY MMBT2222AFSCT-ND
Q3: BSS138; DIGIKEY BSS138CT-ND
R1: 1M; R0805; DIGIKEY 311-1.0MARCT-ND
R2, R4, R14, R15, R22, R23, R24: 10k; R0805; DIGIKEY 311-10.0KCRCT-ND
R3, R5, R10, R11, R12: 1k; R0805; DIGIKEY 311-1.0KARCT-ND
R6, R8, R19: 4.7k; R0805; DIGIKEY 311-4.7KARCT-ND
R7, R13: 2.2k; R0805; DIGIKEY 311-2.2KARCT-ND
R9: 390; R0805; DIGIKEY 311-390ARCT-ND
R16, R20: 100k; R0805; DIGIKEY 311-100KCRCT-ND
R17, R21: 47k; R0805; DIGIKEY 311-47.0KCRCT-ND
R18: 100; R0805; DIGIKEY 311-100ARCT-ND
S1: TAC_SWITCHSMD; TACTILE_SWITCH_SMD; DIGIKEY CKN9104CT-ND
SG1: BUZZERNS; BUZZER-12MM-NS; DIGIKEY 102-1155-ND
SH11: ARDUINO_R3_SHIELD; UNO_R3_SHIELD
SV1: MA03-1; DIGIKEY 952-2264-ND
U3: UBLOX_MAX
U4: LM1086; TO263; DIGIKEY LM1086ISX-5.0/NOPBCT-ND
U5: RADIOMETRIX-HX1
U6: V_REG_LDOSMD; SOT23-5; DIGIKEY LP3985IM5-3.3/NOPBCT-ND
U7: ATMega328; TQFP32-08; DIGIKEY ATMEGA328P-15AZCT-ND
U8: BMP180
U9: LMV324M; SO14; DIGIKEY MCP6L04T-E/SLCT-ND
X1: BU-SMA-H; DIGIKEY CONSMA001-ND
Y1: 16MHz; RESONATOR-SMD; DIGIKEY 478-5420-1-ND

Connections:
9_V_RESET: U3.9_V_RESET
+3V3: C20.1, C21.+, C22.1, Q3.G, R6.2, R19.2, R22.2, SH11.3.3V, U3.6_V_BCKP, U3.7_VCC_IO, U3.8_VCC, U6.5 (OUT), U8.2 (VDD), U8.3 (VDDIO)
+5V: C13.1, C14.+, C15.1, C16.1, C17.1, C18.1, D1.C, L4.1, L7.2, R2.2, R14.1, R23.2, R24.1, SG1.+ (1), SH11.5V, U4.2 (OUT), U6.1 (IN), U6.3 (EN), U7.4 (VCC), U7.6 (VCC), U7.18 (AVCC), U9.4 (V+)
ADC2: SH11.A2, U7.25 (PC2(ADC2))
ADC3: SH11.A3, U7.26 (PC3(ADC3))
ANA-RX-AUD: C9.2, R14.2, R15.1, SH11.A0, U7.23 (PC0(ADC0))
AUD-ANNUNC: R3.1, SH11.D5 (*D5), U7.9 (PD5(T1))
BATT-SENSE: C10.1, R16.1, R17.2, SH11.A1, U7.24 (PC1(ADC1))
D4: SH11.D4, U7.2 (PD4(XCK/T0))
D6: SH11.D6 (*D6), U7.10 (PD6(AIN0))
DIG-PTT: L8.2, R11.1, R12.1, U7.32 (PD2(INT0))
GND: C1.2, C2.2, C4.2, C6.2, C8.2, C10.2, C11.2, C12.2, C13.2, C14.-, C15.2, C16.2, C17.2, C18.2, C19.2, C20.2, C21.-, C22.2, C23.2, C24.2, J1.GND (GNDBREAK), J1.P$4 (GND), J2.4, LED1.C, LED2.C, Q1.E, Q2.E, R15.2, R17.1, R20.2, S1.1, S1.2, SH11.GND@0 (GND), SH11.GND@1 (GND), SH11.GND@2 (GND), SV1.3, U3.1_GND, U3.10_GND, U3.12_GND, U4.1 (GND), U5.0V, U6.2 (GND), U7.3 (GND), U7.5 (GND), U7.21 (GND), U8.7 (GND), U9.11 (V-), U9.12 (+IN), U9.13 (-IN), Y1.2
GPS-RX: Q3.D, R23.1, SH11.D8, U7.12 (PB0(ICP))
GPS-TX: R21.2, SH11.D7, U7.11 (PD7(AIN1))
MISO: SH11.D12, U7.16 (PB4(MISO))
MOSI: SH11.D11 (*D11), U7.15 (PB3(MOSI/OC2))
unnamed: C2.1, R4.2, U9.3 (+IN)
unnamed: R7.1, U9.1 (OUT), U9.2 (-IN)
unnamed: C3.2, R7.2, R8.1
unnamed: C4.1, R8.2, U9.5 (+IN)
unnamed: C3.1, R9.1, U9.6 (-IN), U9.7 (OUT)
unnamed: C5.2, R9.2, R10.1
unnamed: C6.1, R10.2, U9.10 (+IN)
unnamed: D2.A, J1.VIN0 (PWR)
unnamed: D1.A, Q1.C, SG1.- (2)
unnamed: C12.1, L6.2, R18.2
unnamed: C5.1, C7.1, U9.8 (OUT), U9.9 (-IN)
unnamed: U5.RFOUT, X1.1
unnamed: R4.1, U7.1 (PD3(INT1))
unnamed: Q3.S, R22.1, U3.2_TXD1
unnamed: R20.1, R21.1, U3.3_RXD1
unnamed: ANT1.FEED, U3.11_RF_IN
unnamed: R1.1, U7.8 (PB7(XTAL2/TOSC2)), Y1.3
unnamed: C24.1, Q2.B, R12.2
unnamed: LED2.A, R11.2
unnamed: LED1.A, R5.2
unnamed: Q1.B, R3.2
unnamed: L6.1, U5.TXD
unnamed: L7.1, U5.VCC
unnamed: L8.1, U5.EN
unnamed: J2.1, L1.2
unnamed: J2.2, L2.2
unnamed: J2.3, L3.2
unnamed: J2.5, L4.2
unnamed: J2.6, L5.2
unnamed: C1.1, U7.20 (AREF)
unnamed: C19.1, U6.4 (BP)
unnamed: R1.2, U7.7 (PB6(XTAL1/TOSC1)), Y1.1
PTT: C8.1, L2.1, Q2.C, R13.1
RESET: R2.1, S1.3, S1.4, SH11.D10 (*D10), U7.29 (PC6(/RESET))
RFGND: U5.RFGND, U5.RFGND2, X1.2, X1.3 (2), X1.4 (2), X1.5 (2)
RX-AUDIO: C9.1, L3.1
RXD: SH11.RX, SV1.1, U7.30 (PD0(RXD))
SCK: R5.1, SH11.D13, U7.17 (PB5(SCK))
SCL: R6.1, SH11.A5, U7.28 (PC5(ADC5/SCL)), U8.5 (SCL)
SDA: R19.1, SH11.A4, U7.27 (PC4(ADC4/SDA)), U8.6 (SDA)
TNC-TX: SH11.D9 (*D9), U7.14 (PB2(SS/OC1B))
TX-AUDIO: C7.2, C23.1, L1.1, R13.2, R18.1, R24.2
TXD: SH11.TX, SV1.2, U7.31 (PD1(TXD))
V+: C11.1, D2.C, L5.1, R16.2, SH11.VIN, U4.3 (IN)

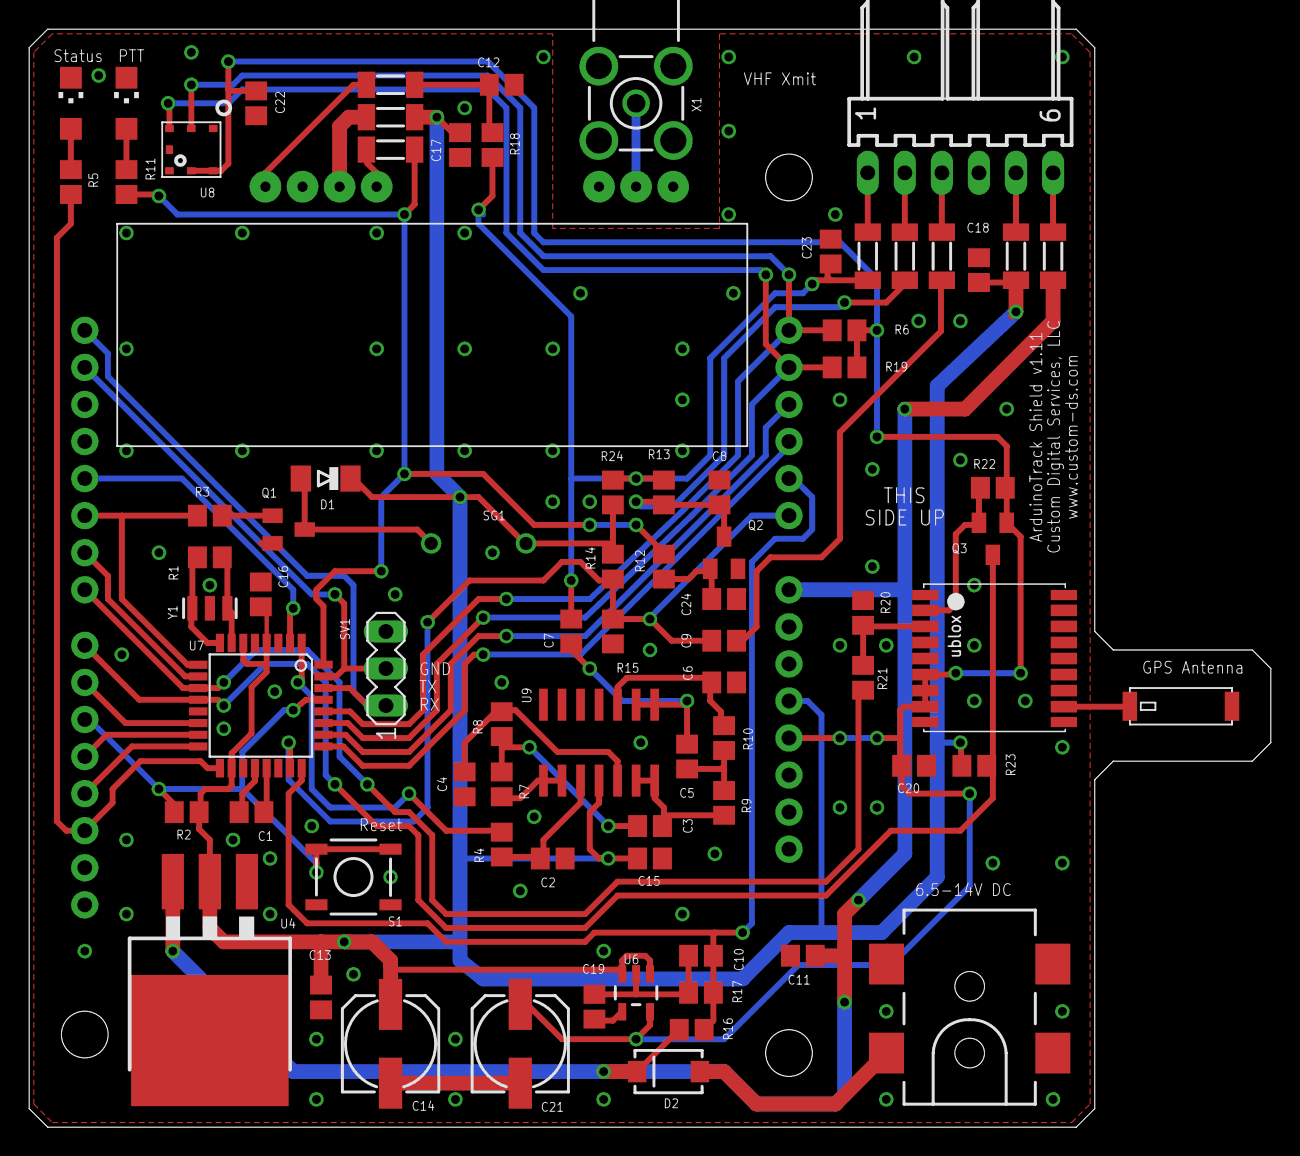
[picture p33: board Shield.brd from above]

Board: 2 copper layers, 85.1 x 75.2 mm, 79 parts (0 on the bottom side), 59 nets.

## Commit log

2016-01-26 Initial commit
    Initial commit of the ArduinoTrack PCB hardware after splitting the
    firmware and hardware repos. The current hardware version is v1.11
    which uses the BMP-180 temp/pressure sensor, as well as the uBlox Max
    M8Q GPS engine.
    [Open Frame for Combined.FCStd, Open Frame for Combined.stl, Open Frame for Shield.FCStd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]
2016-02-08 Minor clean up work to schematic
    Added some values to parts, swapped out the op-amp with a cheaper
    alternative, added part numbers to HX1 and Ublox GPS. Generated a fresh
    BOM, and cleaned up some old files.
    [Shield BOM.csv, Shield.brd, Shield.sch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]
2016-04-10 Working on assembly instructions

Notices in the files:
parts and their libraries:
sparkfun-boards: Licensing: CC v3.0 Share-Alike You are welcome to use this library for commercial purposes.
